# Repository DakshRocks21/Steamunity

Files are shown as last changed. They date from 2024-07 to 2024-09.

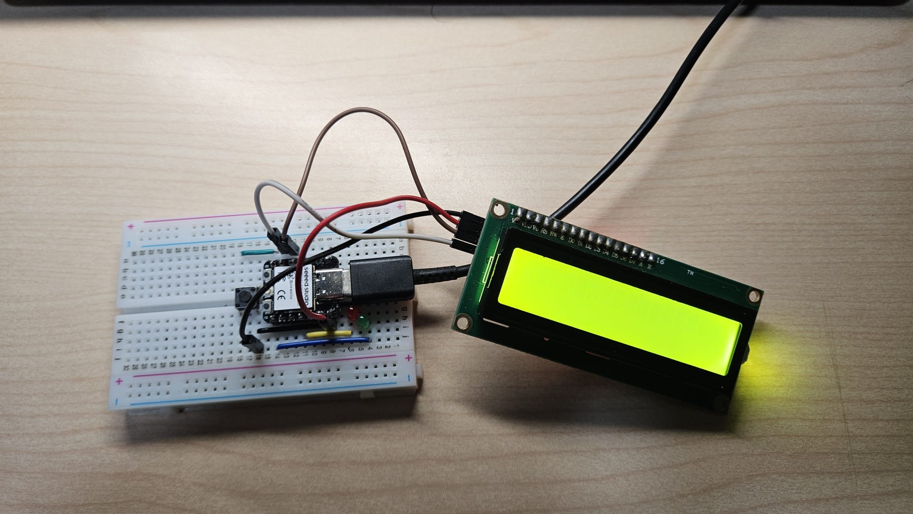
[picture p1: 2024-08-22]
Circuit Layouts/up_to_date/Doorbell/doorbell_assembled_22aug.jpg

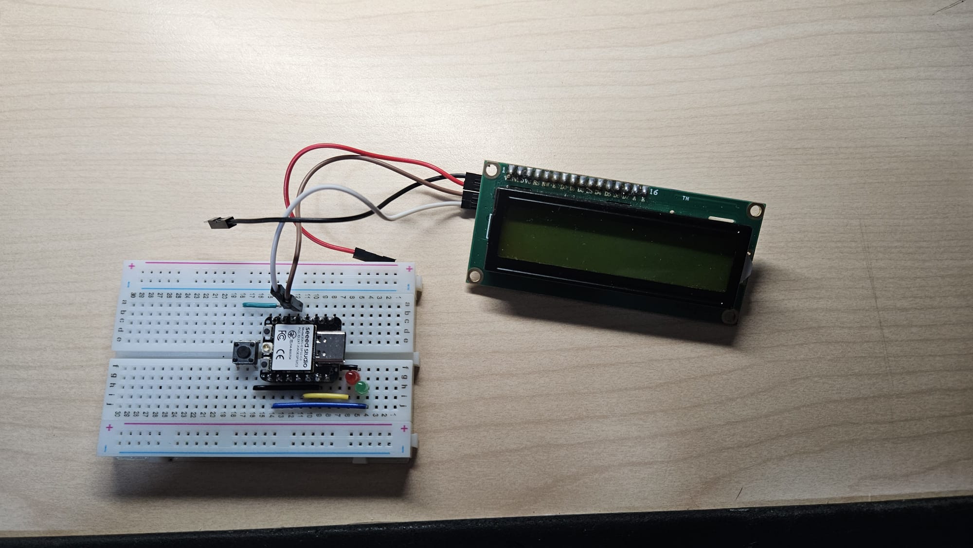
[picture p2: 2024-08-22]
Circuit Layouts/up_to_date/Doorbell/doorbell_not_assembled_22aug.jpg

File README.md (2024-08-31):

# Steamunity 2024: Creating a Doorbell System for elderlies with Hearing Impairments
Welcome! This is a project made for the Steamunity: Design for Community Challenge hosted by SUTD, Singapore. \
Our group consists of Daksh, Jarrett, Jason, Xiu Ling, Tiffany, and Richard, and we have designed an innovate doorbell system to help elderlies who have hearing impairments.

### A Deeper Dive into the Problem
Out of the 15 problem statements offered by the competition organisers, our group chose to work with Chinatown Active Aging Center (AAC) to create a product to help seniors in the area. 

The AAC provides support for seniors in the area through community engagement and befriending activities, and one aspect of these services include home visits. However, a sizable portion of their beneficiaries encounter hearing issues due to their old age, and social workers from Chinatown AAC face difficulty getting them to answer the door, sometimes waiting outside for as long as 30 minutes. It frustrates them greatly and prevents elderlies to receive the support they deserve, and our group aims to improve communication between the two parties with our custom-made doorbell.

### We thus present... DUO
Duo is named as such for not just one, but two reasons:
1. Duo consists of two main components, the doorbell and a wristband. Whenever Duo's doorbell is pressed, it sends a signal to the wristband and activates it, sending visual, audio and vibration cues, compelling wearers to answer the door swiftly. Furthermore, the doorbell comes with a screen! It keeps visitors in the know on whether the homeowner has acknowledged, and likewise, the wristband comes with an acknowledge button. 
2. We designed this product with not just the elderly residents in mind, but also visitors; the acknowledgement feature lets visitors know whether the elderly is on their way to the door and reduces frustrations they might face.

Duo makes use of ESPs (ESP Wemos Lolin and Seeed Xiao C3) to communicate between its various modules using ESP-NOW protocol. It does not use Wifi and makes setting up the system much easier. We also decided to use a range extender in our project (another ESP) that allows the doorbell and wristband to communicate with each other over longer distances, or through more walls.

Ok, cool. The solution works. But what if the elderlies do not want to use it? 

Our team's aware that some elderlies just don't like wearing a wristband all the time when they're at home. That's all right! We designed the wristband to be loud and flashy enough to catch the elderly's attention even if its not strapped to their wrist. (So long as they place it near enough to them, like a bedside table, it _should_ be fine :D )

### Room for Improvement
This product is a rough prototype made for ***Round 1*** of this competition, meaning there's a second round! Our group intends to join this, where our product will be refined and scaled up to something that's actually implementable in the community. And I personally love that idea. \
Here's some cool things we aim to do:
- More customisability: Ringtone, Volume, Vibration Strength, Doorbell Screen Messages, etc. the list goes on
- More features: Making the wristband look and work more like a smartwatch, so the elderlies are more likely to use it on a daily basis
- Backups: We'll refine the backup attention grabber feature thingy whatever it is (like if they are rly stubborn and STILL don't want to use the wristband)
- And we'll conduct more research and make our design sleeker and cooler overall.
You get the gist.

### Misc. References
Decided to keep these here cause why not, lol \
More about AACs in Singapore: https://supportgowhere.life.gov.sg/services/SVC-AACAAACHASACS/active-ageing-centres-aac \
Buzzer Music Tutorial: https://esp32io.com/tutorials/esp32-piezo-buzzer \
LCD Screen Tutorial: https://www.youtube.com/watch?v=COssWn4Pcm4 \
Subway Surfers Ringtone: https://github.com/hibit-dev/buzzer/blob/master/src/movies/subway_surfers/subway_surfers.ino

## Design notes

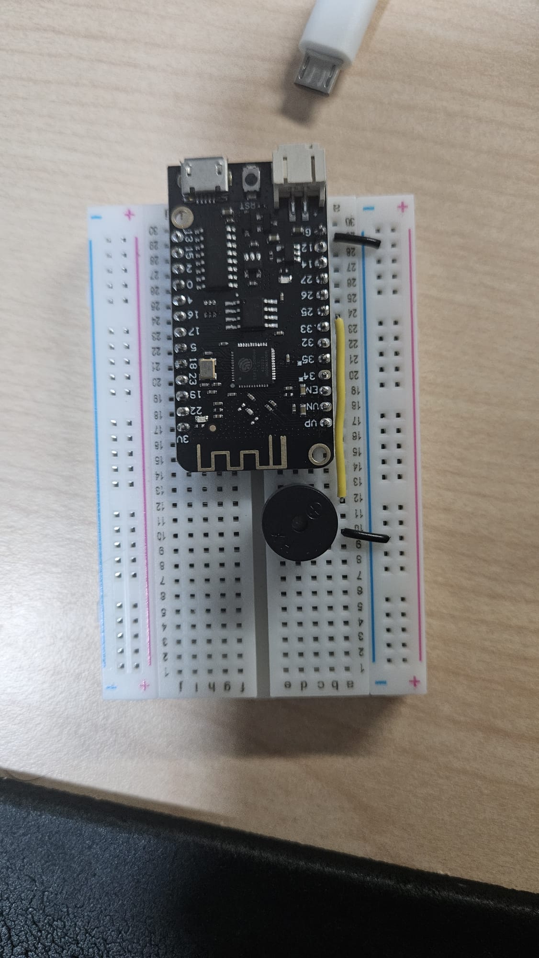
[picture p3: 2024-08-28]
Circuit Layouts/up_to_date/Range Extender/extender_28aug.jpg

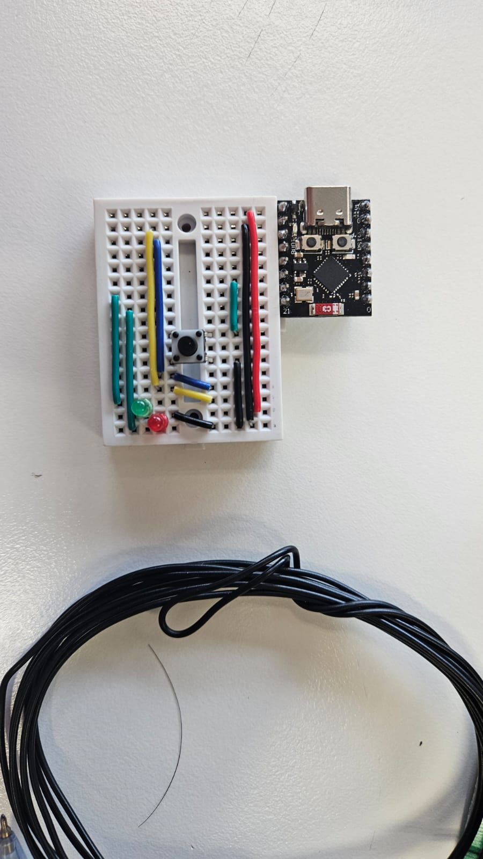
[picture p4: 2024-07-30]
Circuit Layouts/doorbell_new_layout.jpg

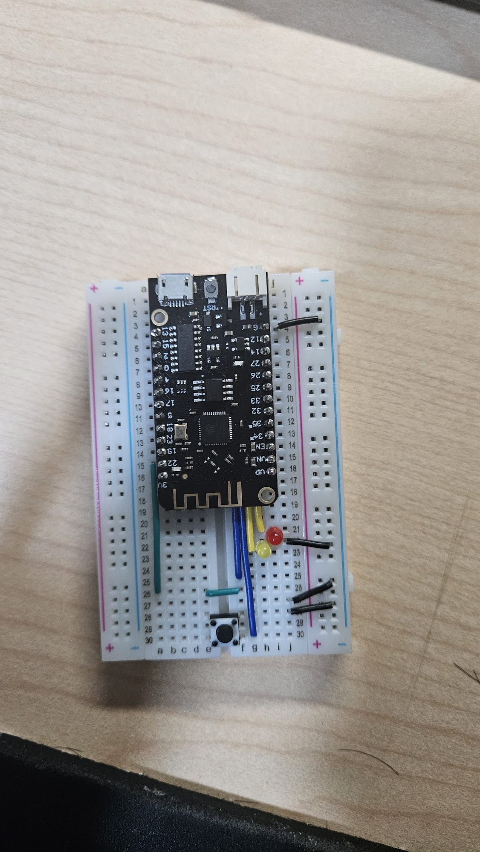
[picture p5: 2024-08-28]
Circuit Layouts/up_to_date/Wristband/wristband_with_esp_28aug.jpg

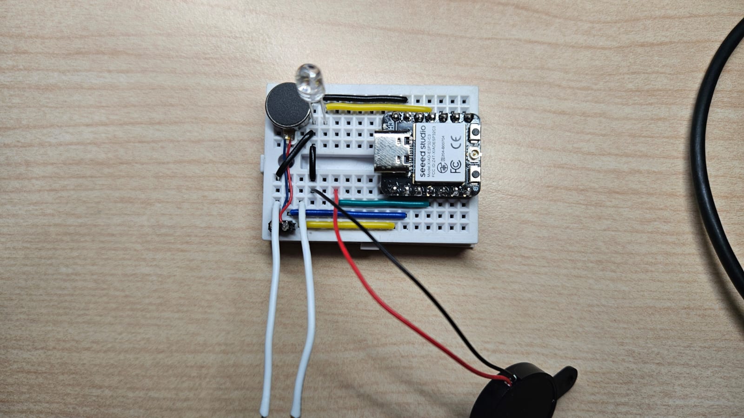
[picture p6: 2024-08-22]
Circuit Layouts/up_to_date/Wristband/wristband_22aug.jpg

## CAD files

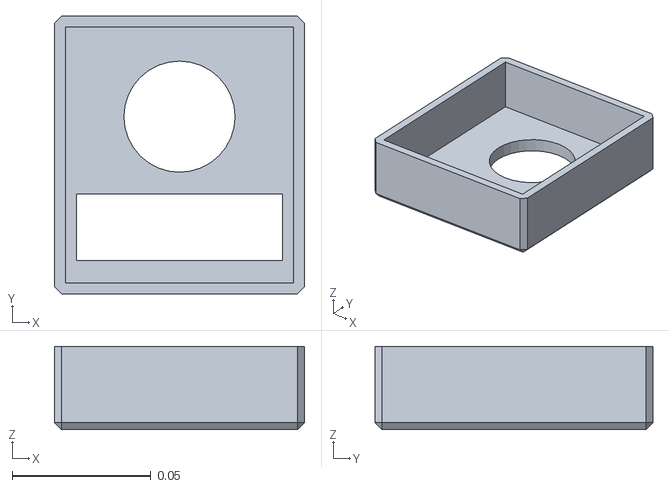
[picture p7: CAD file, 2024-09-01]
3D Models/barry_facedown_front.stl
0.09 x 0.1 x 0.03

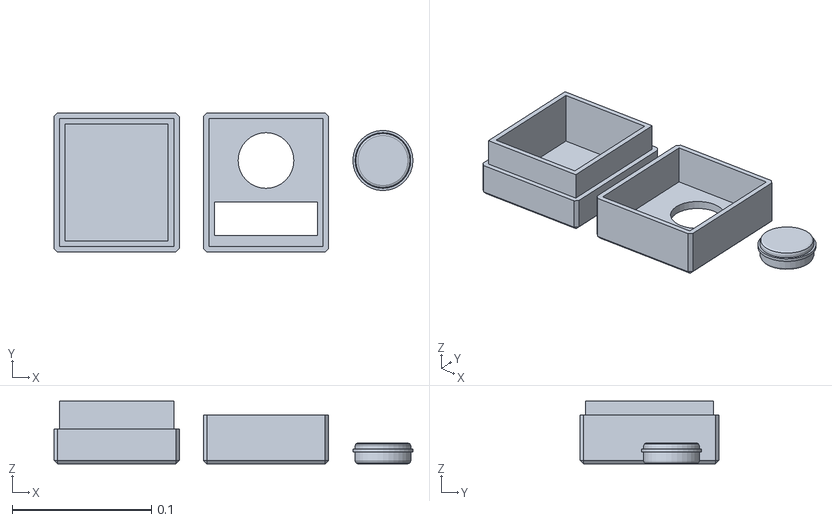
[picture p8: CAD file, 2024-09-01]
3D Models/barry.stl
0.258 x 0.1 x 0.045

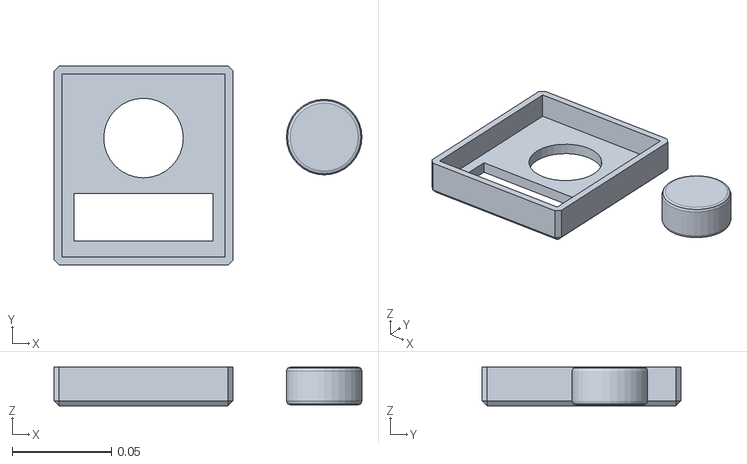
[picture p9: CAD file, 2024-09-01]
3D Models/rizzbuzz_face.stl
0.155 x 0.1 x 0.0195

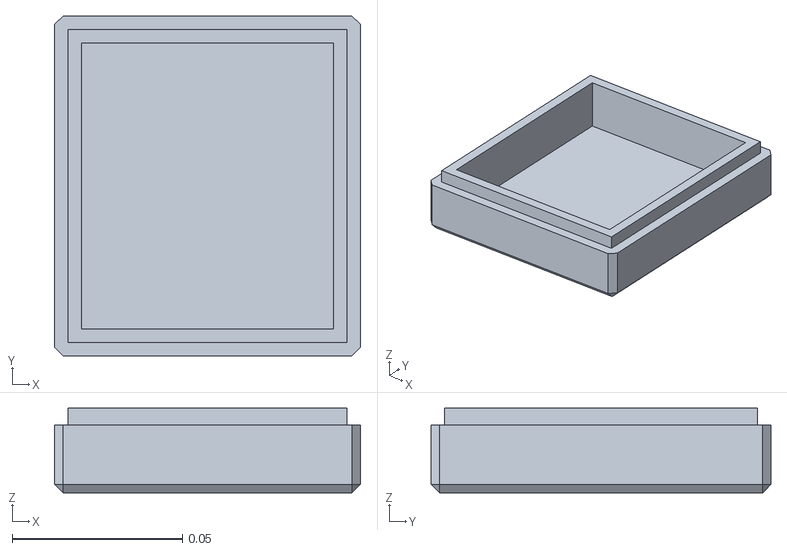
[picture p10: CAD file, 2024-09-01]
3D Models/barry_facedown_back.stl
0.09 x 0.1 x 0.025

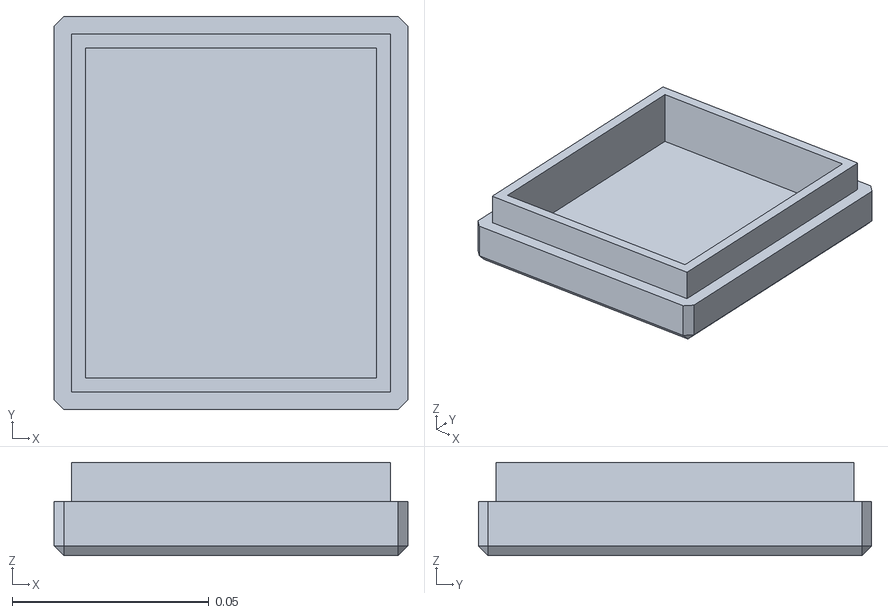
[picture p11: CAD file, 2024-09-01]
3D Models/duo_backface.stl
0.09 x 0.1 x 0.0238

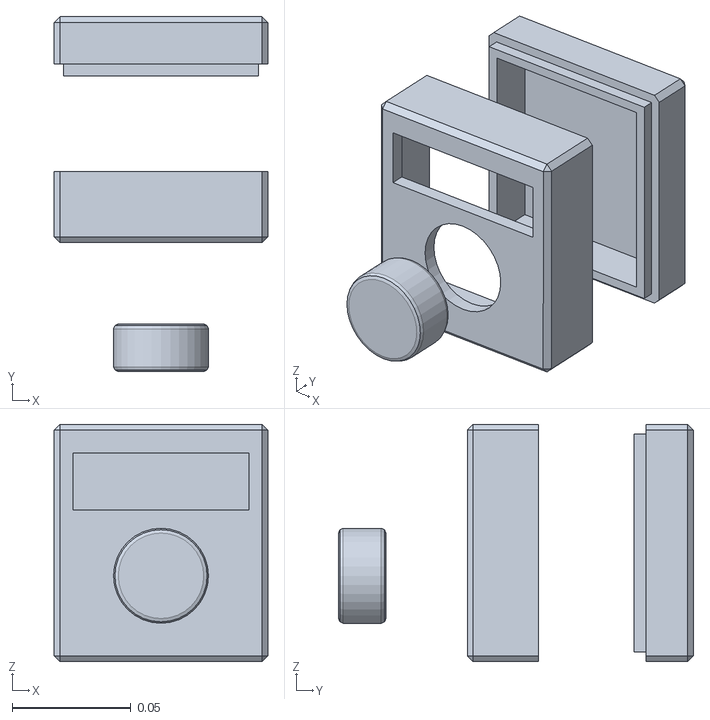
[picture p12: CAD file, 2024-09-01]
3D Models/rizzbuzz.stl
0.09 x 0.15 x 0.1

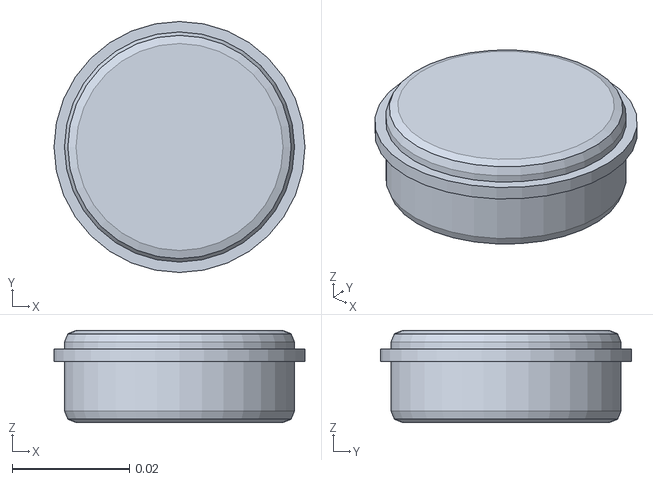
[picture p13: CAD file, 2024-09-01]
3D Models/duo_button.stl
0.0428 x 0.0428 x 0.0157

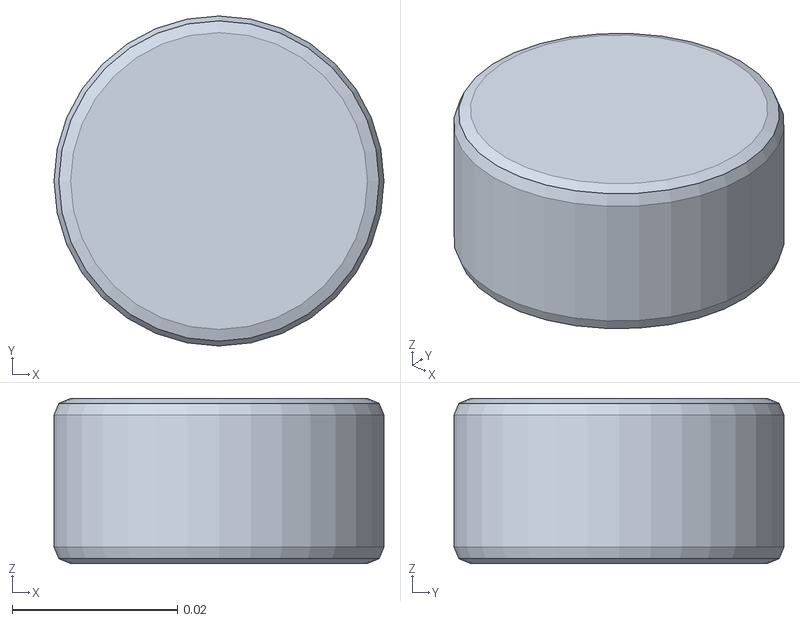
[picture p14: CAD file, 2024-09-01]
3D Models/barry_facedown_button.stl
0.04 x 0.04 x 0.02

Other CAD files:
3D Models/rizzbuzz_face.blend

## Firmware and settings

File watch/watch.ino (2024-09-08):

#include <esp_now.h>
#include <WiFi.h>
#include "pitches.h"

uint8_t rangeExtenderAddress[] = { 0x08, 0xf9, 0xe0, 0xf6, 0xe9, 0xe4 };//mini{0xEC,0x64,0xc9,0x98,0x7e,0x10}; /* Range extender MAC address */ 

int melody[] = {
  NOTE_E5, NOTE_D5, NOTE_FS4, NOTE_GS4, 
  NOTE_CS5, NOTE_B4, NOTE_D4, NOTE_E4, 
  NOTE_B4, NOTE_A4, NOTE_CS4, NOTE_E4,
  NOTE_A4
};

int noteDurations[] = {
  8, 8, 4, 4,
  8, 8, 4, 4,
  8, 8, 4, 4,
  2
};

// Defining Pins - for the Mini, 2, 8 and 9 are reserved for boot modes -> avoid using
const int buttonPin = D0; //12 for ESP, D0 for Mini
const int ledPin = D10; //33 for ESP, D10 for Mini
const int ledPinAlt = D7; //7 for ESP, D7 for Mini
const int buzzerPin = D3; //25 for ESP, D3 for Mini
const int motorPin = D1; // 22 for ESP, D1 for Mini
bool buttonPressed = false;
bool lightOnReceived = false;
bool ackSent = false;

typedef struct struct_message {
  char message[32];
} struct_message;

struct_message myData;
struct_message receivedData;

esp_now_peer_info_t peerInfo;

void OnDataSent(const uint8_t *mac_addr, esp_now_send_status_t status) {
  Serial.print("\r\nLast Packet Send Status:\t");
  Serial.println(status == ESP_NOW_SEND_SUCCESS ? "Delivery Success" : "Delivery Fail");
}

void OnDataRecv(const esp_now_recv_info *info, const uint8_t *incomingData, int len) {
  memcpy(&receivedData, incomingData, sizeof(receivedData));
  Serial.print("Bytes received: ");
  Serial.println(len);
  Serial.print("Message: ");
  Serial.println(receivedData.message);
  Serial.println();

  if (strcmp(receivedData.message, "LIGHT ON") == 0) {
    lightOnReceived = true;
    digitalWrite(ledPin, HIGH);
    digitalWrite(motorPin, HIGH);  // Turn on the vibration motor
    ackSent = false;
  }
}

volatile unsigned long lastDebounceTime = 0;
const unsigned long debounceDelay = 500; // Debounce delay in milliseconds

void IRAM_ATTR handleButtonPress() {
  unsigned long currentTime = millis();
  
  if (currentTime - lastDebounceTime > debounceDelay) {
    buttonPressed = true; 
    lastDebounceTime = currentTime; 
  }
}

void setup() {
  pinMode(buzzerPin, OUTPUT);
  pinMode(ledPin, OUTPUT);
  pinMode(ledPinAlt, OUTPUT);
  pinMode(motorPin, OUTPUT); // Set vibration motor pin as output

  Serial.begin(115200);

  WiFi.mode(WIFI_STA);

  if (esp_now_init() != ESP_OK) {
    Serial.println("Error initializing ESP-NOW");
    return;
  }

  esp_now_register_send_cb(OnDataSent);
  esp_now_register_recv_cb(OnDataRecv);

  memcpy(peerInfo.peer_addr, rangeExtenderAddress, 6);
  peerInfo.channel = 0;
  peerInfo.encrypt = false;

  if (esp_now_add_peer(&peerInfo) != ESP_OK) {
    Serial.println("Failed to add peer");
    return;
  }

  pinMode(buttonPin, INPUT_PULLUP);
  attachInterrupt(digitalPinToInterrupt(buttonPin), handleButtonPress, FALLING);
}

void loop() {
  if (buttonPressed && lightOnReceived && !ackSent) {
    buttonPressed = false;
    lightOnReceived = false;

    strcpy(myData.message, "ACK");

    esp_err_t result = esp_now_send(rangeExtenderAddress, (uint8_t *)&myData, sizeof(myData));

    if (result == ESP_OK) {
      Serial.println("ACK sent with success");
      ackSent = true;
    } else {
      Serial.println("Error sending the ACK");
    }
  }
  if (lightOnReceived) {  
    digitalWrite(motorPin, HIGH);  

    unsigned long previousMillis = 0;
    const long interval = 250; 
    bool ledState = false;

    for (int thisNote = 0; thisNote < sizeof(melody) / sizeof(melody[0]); thisNote++) {
      int noteDuration = 1000 / noteDurations[thisNote];
      tone(buzzerPin, melody[thisNote], noteDuration);
      int pauseBetweenNotes = noteDuration * 1.30;
      
      unsigned long currentMillis = millis();
      if (currentMillis - previousMillis >= interval) {
        previousMillis = currentMillis;
        ledState = !ledState;
        digitalWrite(ledPin, ledState ? HIGH : LOW);
        digitalWrite(ledPinAlt, ledState ? LOW : HIGH);
      }

      delay(pauseBetweenNotes);
      noTone(buzzerPin);
      if (buttonPressed) {
        digitalWrite(ledPin, LOW);
        digitalWrite(ledPinAlt, LOW);
        digitalWrite(motorPin, LOW); // Turn off the vibration motor
        noTone(buzzerPin);
        break;
      }
    }
  }
}

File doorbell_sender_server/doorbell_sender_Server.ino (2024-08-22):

#include <esp_now.h>
#include <WiFi.h>
#include <LiquidCrystal_I2C.h>

LiquidCrystal_I2C lcd(0x27, 16, 2);  // I2C address 0x27, 16 columns and 2 rows

uint8_t broadcastAddress1[] = { 0xEC, 0x64, 0xC9, 0x98, 0x79, 0x5C };  // Replace with your actual receiver MAC Address

const int buttonPin = 26; // 26 for Esp, 2 for Mini
bool buttonPressed = false;
unsigned long lastSendTime = 0;
const unsigned long sendTimeout = 15000;  // 15 seconds timeout
const int toAccept = 25; // 25 for Esp, 21 for Mini (red LED)
const int accepted = 33; // 33 for Esp, 20 for Mini (green LED)
const int sdaPin = 23; // 23 for Esp, 6 for Mini
const int sclPin = 19; // 19 for Esp, 7 for Mini

typedef struct struct_message {
  char message[32];
} struct_message;
struct_message myData;
struct_message receivedData;

esp_now_peer_info_t peerInfo;

void OnDataSent(const uint8_t *mac_addr, esp_now_send_status_t status) {
  Serial.print("\r\nLast Packet Send Status:\t");
  Serial.println(status == ESP_NOW_SEND_SUCCESS ? "Delivery Success" : "Delivery Fail");
}

void OnDataRecv(const esp_now_recv_info *info, const uint8_t *incomingData, int len) {
  memcpy(&receivedData, incomingData, sizeof(receivedData));
  Serial.print("Bytes received: ");
  Serial.println(len);
  Serial.print("Message: ");
  Serial.println(receivedData.message);
  Serial.println();

  digitalWrite(accepted, HIGH);
  digitalWrite(toAccept, LOW);

  lcd.clear();
  lcd.setCursor(0, 0);
  lcd.print("Acknowledged!");
}

void IRAM_ATTR handleButtonPress() {
  buttonPressed = true;
}

void setup() {
  // Initialize light pin
  pinMode(toAccept, OUTPUT);
  pinMode(accepted, OUTPUT);

  // initialize LCD
  Wire.begin(sdaPin, sclPin);  // SDA on GPIO 23, SCL on GPIO 19
  lcd.init();
  lcd.backlight();
  lcd.clear();
  lcd.setCursor(0, 0);
  lcd.print("This took TOO");
  lcd.setCursor(0, 1);
  lcd.print("long to make");

  // Init Serial Monitor
  Serial.begin(115200);

  // Set device as a Wi-Fi Station
  WiFi.mode(WIFI_STA);

  // Init ESP-NOW
  if (esp_now_init() != ESP_OK) {
    Serial.println("Error initializing ESP-NOW");
    return;
  }

  // Register for Send CB to get the status of transmitted packet
  esp_now_register_send_cb(OnDataSent);

  // Register for recv CB to get recv packet info
  esp_now_register_recv_cb(OnDataRecv);

  // Register peer
  memcpy(peerInfo.peer_addr, broadcastAddress1, 6);
  peerInfo.channel = 0;
  peerInfo.encrypt = false;
  if (esp_now_add_peer(&peerInfo) != ESP_OK) {
    Serial.println("Failed to add peer 1");
    return;
  }

  // Initialize button pin as input
  pinMode(buttonPin, INPUT_PULLUP);
  attachInterrupt(digitalPinToInterrupt(buttonPin), handleButtonPress, FALLING);
}

void loop() {
  if (buttonPressed) {
    buttonPressed = false;
    digitalWrite(toAccept, HIGH);

    unsigned long currentTime = millis();
    if (currentTime - lastSendTime >= sendTimeout) {
      lastSendTime = currentTime;

      // Set message to send
      strcpy(myData.message, "LIGHT ON");

      // Send message via ESP-NOW to both peers
      esp_err_t result1 = esp_now_send(broadcastAddress1, (uint8_t *)&myData, sizeof(myData));

      if (result1 == ESP_OK) {
        Serial.println("Sent with success to peers");
        lcd.clear();
        lcd.setCursor(0, 0);
        lcd.print("Calling!");
        lcd.setCursor(0, 1);
        lcd.print("Wait a bit...");
      } else {
        Serial.println("Error sending the data");
      }
    } else {
      Serial.println("Timeout in effect. Please wait before sending again.");
    }
  }
}

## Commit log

2024-07-28 Added pitches.h, made it play a simple tune and stop upon button press
2024-07-28 Fix screen input and make it respond to wireless communication
    [doorbell_sender_Server.ino]
2024-08-02 V1: prototype working
2024-08-22 Added new pin config for Esp Mini
2024-08-22 Added circuit connection pictures for wristband
2024-08-22 Wired up doorbell module
2024-08-27 Reverted MAC addresses to what it was before, and decided to dump the MAC address finder inside
    [Mac_Address_Finder.ino, extender.ino, watch.ino]
2024-08-27 Added Vibration Motor, second LED and relevant code to the watch circuit
    [watch.ino]
2024-08-27 Added buzzer on extender subcircuit, works exactly like the wristband one does
    [extender.ino]
2024-08-28 Ported wristband circuit to the Seeed Xiao Mini, hardware + software wise
2024-08-28 Ported doorbell circuit to the Seeed Xiao Mini, hardware + software wise
2024-08-28 Added new circuit diagrams and Prototype V2 video
2024-09-01 Added debouncing for doorbell button
2024-09-01 fixed bug where wristband would automatically send back ACK upon receiving LIGHT ON signal
    [extender.ino, watch.ino]
2024-09-08 Commented out debugging LEDs for doorbell circuit
2024-09-08 Added video of the final prototype
